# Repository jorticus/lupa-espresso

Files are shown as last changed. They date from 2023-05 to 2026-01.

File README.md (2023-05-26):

# LUPA ESPRESSO

ESP32 firmware for controlling my modified Vibiemme Domobar Junior, which is an E61-grouphead Heat Exchanger (HX) espresso machine.

The main goal is to add some smarts, but retain the manual control and analog feel.

NOTE: This project is not intended to be re-used on other machines as it is highly specific to the particular modifications I have made.

## Features

- PID control of heater boiler
- Automatic brew timer
- Digital pressure / temperature / flow readouts
- Graphing and gauges displayed on two round TFT displays
- Grouphead temperature approximation
- Preheat/sleep states
- Remote control
- HomeAssistant integration

## Modifications

- Analog pressure dials replaced with round TFT displays
- Digital pressure transducer
- Water flow sensor
- Platinum PT100 thermocouple probe
- Boiler SSR controlled by ESP32

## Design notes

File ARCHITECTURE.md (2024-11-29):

# Task Overview

## Core 0 : RF/Radio

## Core 1 : Arduino loop()

### Tasks:

- CoreIO : Priority 3, 1ms tick
  - GPIO handling
  - State machine
  - PID control loops
        
- Network : Priority 2, 10ms tick
  - WiFi reconnection logic
  - MQTT reconnection logic
  - HomeAssistant publishing
  - OTA

- UI : Priority 1
  - Idle loop (exeucte when no other tasks running)
  - Render
  - Display Update

- loop() : Priority 1
  - Failsafe code execution only.

### Timers:

- Timer 1 : 10ms
  - Pressure

- Timer 2 : 100ms
  - Temperature RTD 1 & 2
  - Water Low GPIO
  - Pulse Counter 1 & 2
  - Update graph samples

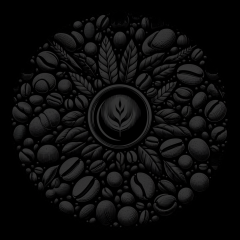
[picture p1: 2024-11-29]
img/RGB565/bean_bg2b.png

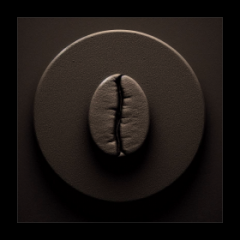
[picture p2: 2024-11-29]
img/RGB565/bg_coffee_eye_2.png

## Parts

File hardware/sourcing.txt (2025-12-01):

High voltage parts:
https://nz.element14.com/vigortronix/vtx-215-005-003/power-supply-ac-dc-3-3v-1a/dp/3870399
https://nz.element14.com/multicomp-pro/mcksk450m100g17s/capacitor-alu-elec-10uf-450v-radial/dp/2610819
https://nz.element14.com/panasonic-electric-works/aqh1213aj/ssr-600v-0-6a/dp/2095712
https://nz.element14.com/schurter/3404-2416-11/fuse-smd-umz-250-1a/dp/1829461
https://nz.element14.com/multicomp-pro/mor03sj0150a19/res-15r-5-3w-axial-metal-oxide/dp/1357899
https://nz.element14.com/kemet/a750kk827m0jaae016/cap-820-f-6-3v-20/dp/2614008

ESP32:
https://www.lcsc.com/product-detail/C328062.html?s_z=n_ESP32-WROOM-32U

Modules:
https://www.aliexpress.com/item/1005006704297164.html MAX RTD temperature converter module
https://www.aliexpress.com/item/1005004962049197.html 2x Round Display
https://www.aliexpress.com/item/4000411199411.html 2x Water flow sensor
https://www.aliexpress.com/item/1005004349225653.html 1x pressure sensor: G1/8 thread, 0-12Bar, I2C Output (or other thread to suit your machine)
https://www.aliexpress.com/item/32954468941.html 2x RTD temperature sensors:
    1x PT100, L 50mm, 1/4"
    1x PT100, L 100mm, 1/4"

Connectors:
https://nz.element14.com/multicomp-pro/mp001801/wtb-conn-header-8pos-1row-2-5mm/dp/3287578
https://nz.element14.com/multicomp-pro/mp001809/wtb-conn-header-r-a-2pos-1row/dp/3287588
https://nz.element14.com/multicomp-pro/mp001797/wtb-conn-header-4pos-1row-2-5mm/dp/3287574
https://nz.element14.com/multicomp-pro/mp001838/contact-socket-crimp-28-22awg/dp/3287624
https://nz.element14.com/multicomp-pro/mp001795/wtb-conn-header-2pos-1row-2-5mm/dp/3287572
https://nz.element14.com/multicomp-pro/mp001829/wtb-housing-rcpt-8pos-1row-2-5mm/dp/3287611
https://nz.element14.com/multicomp-pro/mp001823/wtb-housing-rcpt-2pos-1row-2-5mm/dp/3287603
https://nz.element14.com/multicomp-pro/mp001825/wtb-housing-rcpt-4pos-1row-2-5mm/dp/3287605

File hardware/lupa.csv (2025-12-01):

Reference | Qty | Value | DNP | Exclude from BOM | Exclude from Board | Footprint | Datasheet
C1
C6
C8 | 1 | 820uF 6.3V |  |  |  | Capacitor_THT:CP_Radial_D8.0mm_P3.50mm | ~
C9 | 1 | 1uF |  |  |  | Capacitor_SMD:C_0603_1608Metric | ~
C10 | 1 | 1nF 400V Y |  |  |  | Capacitor_THT:C_Rect_L7.0mm_W2.5mm_P5.00mm | ~
C12 | 1 | 100nF X2 |  |  |  | Capacitor_THT:C_Disc_D4.7mm_W2.5mm_P5.00mm | ~
C13 | 1 | 100uF |  |  |  | Capacitor_THT:CP_Radial_D5.0mm_P2.50mm | ~
C14 | 1 | 10uF 450V |  |  |  | Capacitor_THT:CP_Radial_D10.0mm_P5.00mm | https://4donline.ihs.com/images/VipMasterIC/IC/SCMP/SCMP-S-A0009021038/SCMP-S-A0009021038-1.pdf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
D1 | 1 | SMBJ7A |  |  |  | Diode_SMD:D_SMB | https://www.st.com/resource/en/datasheet/sm6t.pdf
F1 | 1 | 1A 250V |  |  |  | Fuse:Fuse_Schurter_UMZ250 | https://www.farnell.com/datasheets/3975405.pdf
FB1 | 1 | Ferrite |  |  |  | Resistor_SMD:R_0603_1608Metric | ~
J1 | 1 | LEVER |  |  |  | Connector_JST:JST_XH_B2B-XH-A_1x02_P2.50mm_Vertical | ~
J2 | 1 | POWER_BTN |  |  |  | Connector_JST:JST_XH_B2B-XH-A_1x02_P2.50mm_Vertical | ~
J3 | 1 | LOW_WATER |  |  |  | Connector_JST:JST_XH_B2B-XH-A_1x02_P2.50mm_Vertical | ~
J4 | 1 | FLOW1 |  |  |  | Connector_JST:JST_XH_B4B-XH-A_1x04_P2.50mm_Vertical | ~
J5 | 1 | FLOW2 |  |  |  | Connector_JST:JST_XH_B4B-XH-A_1x04_P2.50mm_Vertical | ~
J6 | 1 | PRESSURE1 |  |  |  | Connector_JST:JST_XH_B4B-XH-A_1x04_P2.50mm_Vertical | ~
J7 | 1 | PRESSURE2 |  |  |  | Connector_JST:JST_XH_B4B-XH-A_1x04_P2.50mm_Vertical | ~
J8 | 1 | LCD_L |  |  |  | Connector_JST:JST_XH_B8B-XH-A_1x08_P2.50mm_Vertical | ~
J9 | 1 | LCD_R |  |  |  | Connector_JST:JST_XH_B8B-XH-A_1x08_P2.50mm_Vertical | ~
J10 | 1 | LED_PWR |  |  |  | Connector_JST:JST_XH_B2B-XH-A_1x02_P2.50mm_Vertical | ~
J11 | 1 | MAX31865 |  |  |  | Connector_PinHeader_2.54mm:PinHeader_1x08_P2.54mm_Vertical | ~
J12 | 1 | POWER |  |  |  | Connector_JST:JST_XH_B2B-XH-A_1x02_P2.50mm_Vertical | ~
J13 | 1 | PROG |  |  |  | Connector_PinHeader_2.54mm:PinHeader_1x06_P2.54mm_Vertical_SMD_Pin1Left | ~
J14 | 1 | BOILER_SSR |  |  |  | Connector_JST:JST_XH_S2B-XH-A_1x02_P2.50mm_Horizontal | ~
J15
J16 | 1 | Mains |  |  |  | TerminalBlock_Altech:Altech_AK300_1x03_P5.00mm_45-Degree | ~
J17 | 1 | Fill Solenoid |  |  |  | TerminalBlock_Altech:Altech_AK300_1x02_P5.00mm_45-Degree | ~
J18 | 1 | Pump |  |  |  | TerminalBlock_Altech:Altech_AK300_1x02_P5.00mm_45-Degree | ~
J19 | 1 | Water Level |  |  |  | Connector_JST:JST_XH_B2B-XH-A_1x02_P2.50mm_Vertical | ~
L1 | 1 | 4.7mH |  |  |  | Inductor_THT:L_Radial_D6.0mm_P4.00mm | ~
L2 | 1 | 4.7uH 2.2A |  |  |  | Inductor_SMD:L_6.3x6.3_H3 | ~
Q1 | 1 | 2N7002 |  |  |  | Package_TO_SOT_SMD:SOT-23 | https://www.onsemi.com/pub/Collateral/NDS7002A-D.PDF
R1 | 1 | 10R |  |  |  | Resistor_SMD:R_0603_1608Metric | ~
R2
R5
R8
R16 | 1 | 12R 3W |  |  |  | Resistor_THT:R_Axial_DIN0516_L15.5mm_D5.0mm_P5.08mm_Vertical | https://www.farnell.com/datasheets/3110733.pdf
R22
RV1 | 1 | MOV |  |  |  | Capacitor_THT:C_Disc_D4.7mm_W2.5mm_P5.00mm
U1 | 1 | ESP32-WROOM-32U |  |  |  | RF_Module:ESP32-WROOM-32U | https://www.espressif.com/sites/default/files/documentation/esp32-wroom-32d_esp32-wroom-32u_datasheet_en.pdf
U2 | 1 | VTX-215-005-003 |  |  |  | Visclib:SMPS-VTX-215-005-003 | https://www.farnell.com/datasheets/3621164.pdf
U3

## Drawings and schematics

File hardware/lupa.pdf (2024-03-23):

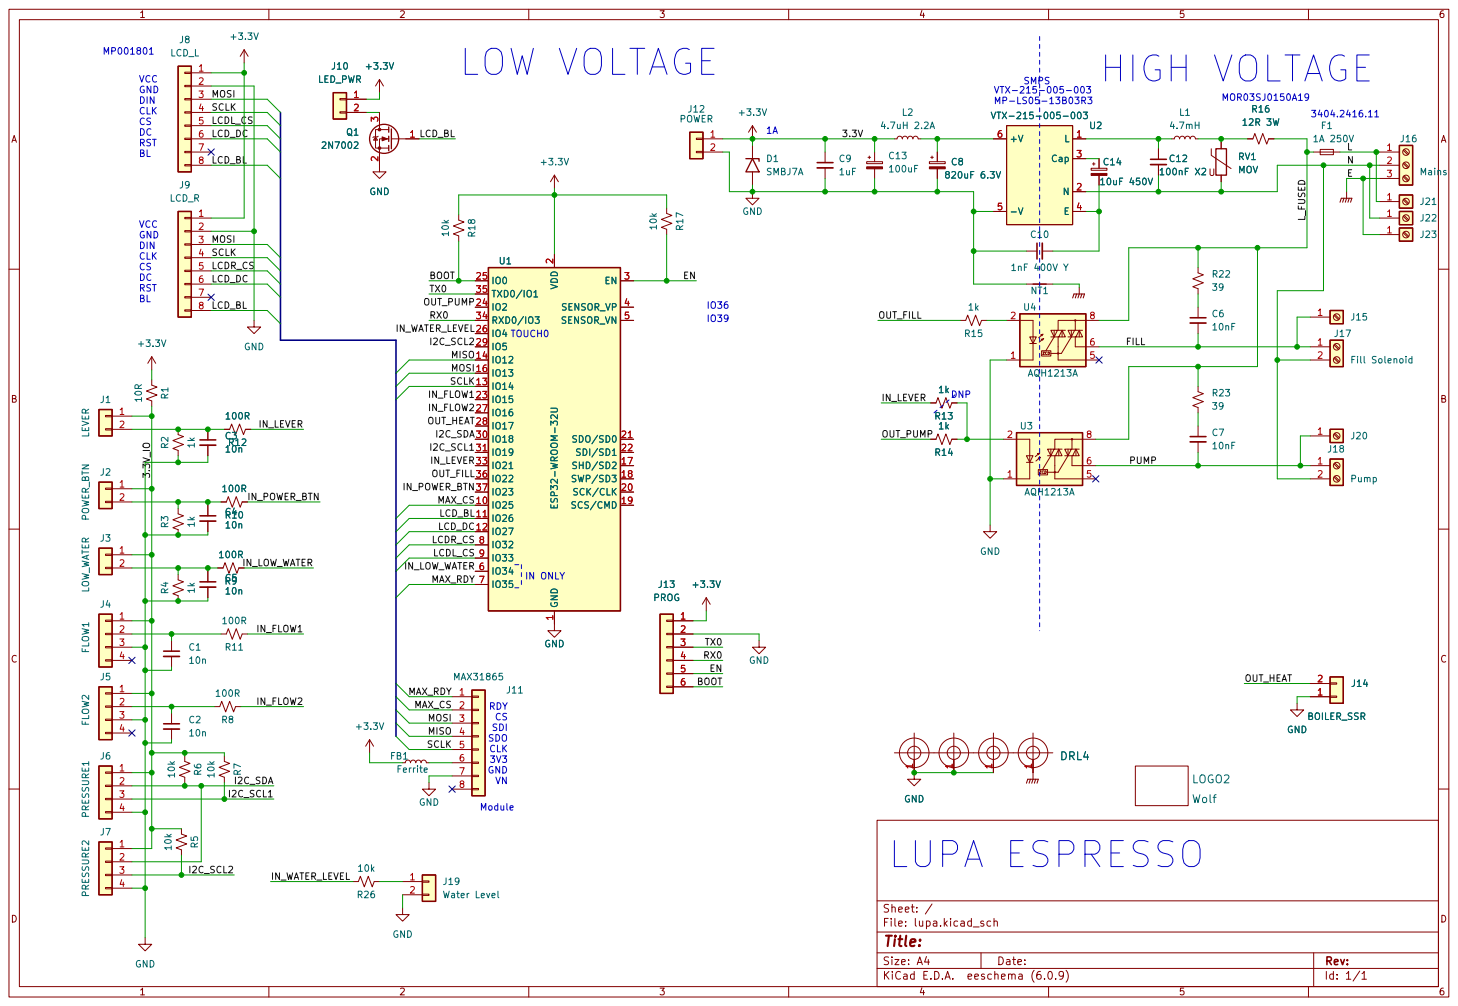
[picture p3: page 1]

SCLK LOW VOLTAGE
VTX-215-005-003 MP-LS05-13B03R3 SMPS LUPA ESPRESSO

2 SCK/CLK 20 SDO/SD0 21 SDI/SD1 22

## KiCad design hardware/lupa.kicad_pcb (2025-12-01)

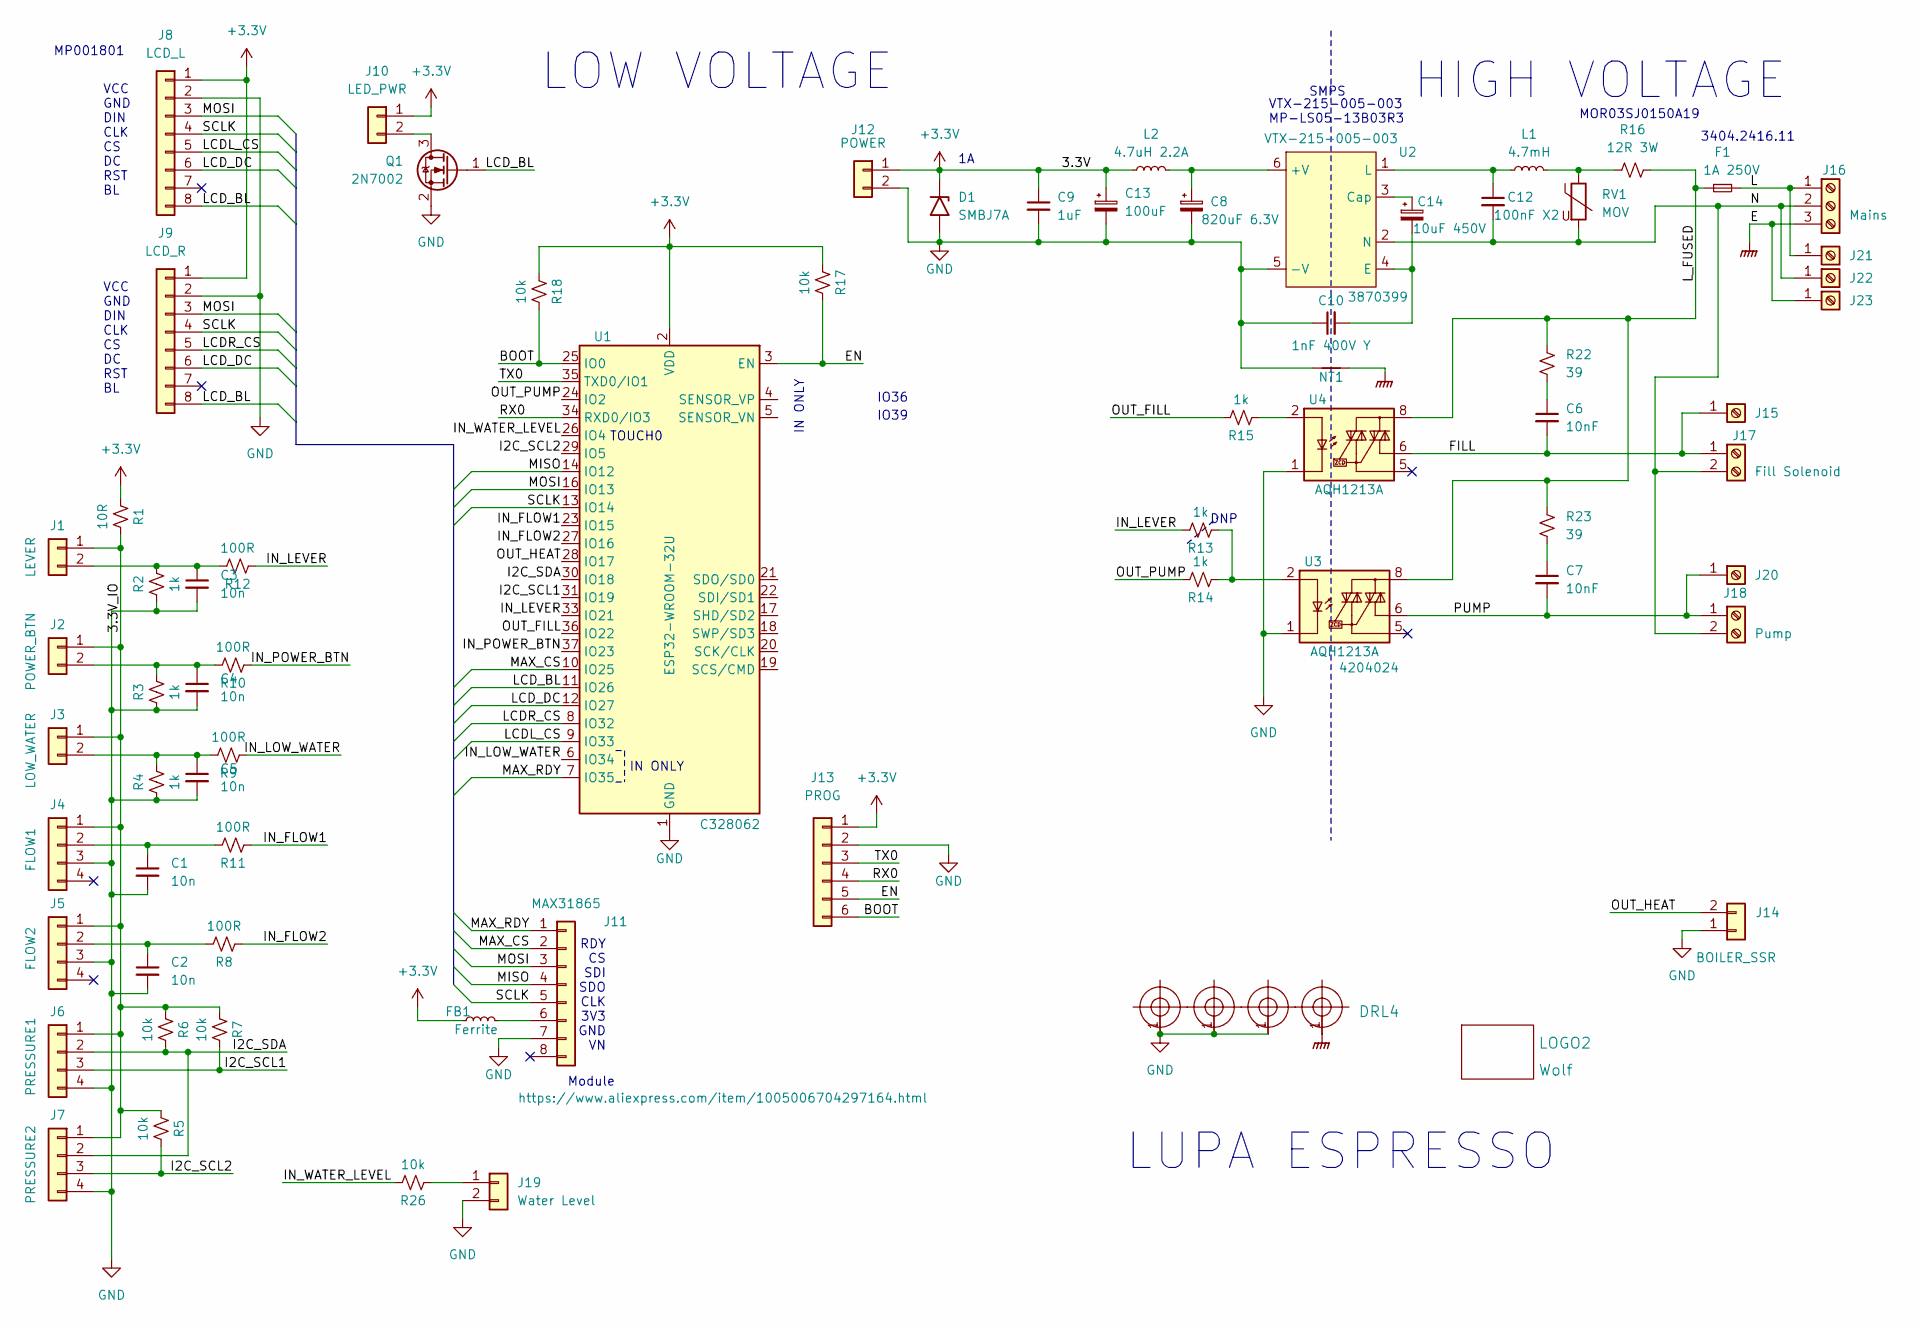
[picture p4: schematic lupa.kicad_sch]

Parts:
C1, C2, C3, C4, C5: 10n; C_0603_1608Metric
C6, C7: 10nF; R_0805_2012Metric
C8: 820uF 6.3V; CP_Radial_D8.0mm_P3.50mm; Farnell 2614008
C9: 1uF; C_0603_1608Metric
C10: 1nF 400V Y; C_Rect_L7.0mm_W2.5mm_P5.00mm
C12: 100nF X2; C_Disc_D4.7mm_W2.5mm_P5.00mm
C13: 100uF; CP_Radial_D5.0mm_P2.50mm
C14: 10uF 450V; CP_Radial_D10.0mm_P5.00mm; Farnell 2610819
D1: SMBJ7A; D_SMB
DRL1, DRL2, DRL3, DRL4: DrillHoleE; MountingHole_3.2mm_M3_Pad
F1: 1A 250V; Fuse_Schurter_UMZ250; Farnell 1829461
FB1: Ferrite; R_0603_1608Metric
J1: LEVER; JST_XH_B2B-XH-A_1x02_P2.50mm_Vertical; Farnell 3287572
J2: POWER_BTN; JST_XH_B2B-XH-A_1x02_P2.50mm_Vertical; Farnell 3287572
J3: LOW_WATER; JST_XH_B2B-XH-A_1x02_P2.50mm_Vertical; Farnell 3287572
J4: FLOW1; JST_XH_B4B-XH-A_1x04_P2.50mm_Vertical; Farnell 3287574
J5: FLOW2; JST_XH_B4B-XH-A_1x04_P2.50mm_Vertical; Farnell 3287574
J6: PRESSURE1; JST_XH_B4B-XH-A_1x04_P2.50mm_Vertical; Farnell 3287574
J7: PRESSURE2; JST_XH_B4B-XH-A_1x04_P2.50mm_Vertical; Farnell 3287574
J8: LCD_L; JST_XH_B8B-XH-A_1x08_P2.50mm_Vertical; Farnell 3287578
J9: LCD_R; JST_XH_B8B-XH-A_1x08_P2.50mm_Vertical; Farnell 3287578
J10: LED_PWR; JST_XH_B2B-XH-A_1x02_P2.50mm_Vertical; Farnell 3287572
J11: MAX31865; PinHeader_1x08_P2.54mm_Vertical
J12: POWER; JST_XH_B2B-XH-A_1x02_P2.50mm_Vertical; Farnell 3287572
J13: PROG; PinHeader_1x06_P2.54mm_Vertical_SMD_Pin1Left
J14: BOILER_SSR; JST_XH_S2B-XH-A_1x02_P2.50mm_Horizontal; Farnell 3287588
J15, J20, J21, J22, J23: Screw_Terminal_01x01; TAB_TERMINAL
J16: Mains; Altech_AK300_1x03_P5.00mm_45-Degree
J17: Fill Solenoid; Altech_AK300_1x02_P5.00mm_45-Degree
J18: Pump; Altech_AK300_1x02_P5.00mm_45-Degree
J19: Water Level; JST_XH_B2B-XH-A_1x02_P2.50mm_Vertical; Farnell 3287572
L1: 4.7mH; L_Radial_D6.0mm_P4.00mm
L2: 4.7uH 2.2A; L_6.3x6.3_H3
LOGO2: Wolf; wolfpaw-0.3
NT1: NetTie_2; NetTie-2_SMD_Pad2.0mm
Q1: 2N7002; SOT-23
R1: 10R; R_0603_1608Metric
R2, R3, R4, R13, R14, R15: 1k; R_0603_1608Metric
R5, R6, R7, R17, R18, R26: 10k; R_0603_1608Metric
R8, R9, R10, R11, R12: 100R; R_0603_1608Metric
R16: 12R 3W; R_Axial_DIN0516_L15.5mm_D5.0mm_P5.08mm_Vertical; Farnell 1357899
R22, R23: 39; R_0805_2012Metric
RV1: MOV; C_Disc_D4.7mm_W2.5mm_P5.00mm
U1: ESP32-WROOM-32U; LCSC C328062
U2: VTX-215-005-003; SMPS-VTX-215-005-003; Farnell 3870399
U3, U4: AQH1213A; SSO-7-8_6.4x9.78mm_P2.54mm; Mouser 769-AQH1213A

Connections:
+3.3V: C9.1, C13.1, D1.1 (A1), FB1.1, J8.1, J9.1, J10.1, J12.1, J13.1, L2.1, R1.1, R17.1, R18.1, U1.2 (VDD)
/3.3V_IO: J1.1, J2.1, J3.1, J4.1, J5.1, J6.1, J7.1, R1.2, R5.1, R6.1, R7.1
/BOOT: J13.6, R18.2, U1.25 (IO0)
/EN: J13.5, R17.2, U1.3 (EN)
/FILL: C6.2, J15.1, J17.1, U4.6
/I2C_SCL1: J6.3, R7.2, U1.31 (IO19)
/I2C_SCL2: J7.3, R5.2, U1.29 (IO5)
/I2C_SDA: J6.2, J7.2, R6.2, U1.30 (IO18)
/IN_FLOW1: R11.1, U1.23 (IO15)
/IN_FLOW2: R8.1, U1.27 (IO16)
/IN_LEVER: R12.1, R13.2, U1.33 (IO21)
/IN_LOW_WATER: R9.1, U1.6 (IO34)
/IN_POWER_BTN: R10.1, U1.37 (IO23)
/IN_WATER_LEVEL: R26.2, U1.26 (IO4)
/L: F1.2, J16.1, J21.1
/LCDL_CS: J8.5, U1.9 (IO33)
/LCDR_CS: J9.5, U1.8 (IO32)
/LCD_BL: J8.8, J9.8, Q1.1 (G), U1.11 (IO26)
/LCD_DC: J8.6, J9.6, U1.12 (IO27)
/L_FUSED: F1.1, R16.2, R22.1, R23.1, U3.8, U4.8
/MAX_CS: J11.2, U1.10 (IO25)
/MAX_RDY: J11.1, U1.7 (IO35)
/MISO: J11.4, U1.14 (IO12)
/MOSI: J8.3, J9.3, J11.3, U1.16 (IO13)
/N: C12.2, J16.2, J17.2, J18.2, J22.1, RV1.2, U2.2 (N)
/OUT_FILL: R15.2, U1.36 (IO22)
/OUT_HEAT: J14.2, U1.28 (IO17)
/OUT_PUMP: R14.2, U1.24 (IO2)
/PUMP: C7.2, J18.1, J20.1, U3.6
/RX0: J13.4, U1.34 (RXD0/IO3)
/SCLK: J8.4, J9.4, J11.5, U1.13 (IO14)
/TX0: J13.3, U1.35 (TXD0/IO1)
GND: C1.2, C2.2, C3.2, C4.2, C5.2, C8.2, C9.2, C10.1, C13.2, D1.2 (A2), DRL1.1, DRL2.1, DRL3.1, J4.3, J5.3, J6.4, J7.4, J8.2, J9.2, J11.7, J12.2, J13.2, J14.1, J19.2, NT1.1, Q1.2 (S), R2.1, R3.1, R4.1, U1.1 (GND), U1.15 (GND), U1.38 (GND), U1.39 (GND), U2.5 (-V), U3.1, U3.3, U3.4, U4.1, U4.3, U4.4
GNDPWR: DRL4.1, J16.3, J23.1, NT1.2
unnamed: C6.1, R22.2
unnamed: C7.1, R23.2
unnamed: C3.1, J1.2, R2.2, R12.2
unnamed: C4.1, J2.2, R3.2, R10.2
unnamed: C5.1, J3.2, R4.2, R9.2
unnamed: C1.1, J4.2, R11.2
unnamed: C2.1, J5.2, R8.2
unnamed: J10.2, Q1.3 (D)
unnamed: FB1.2, J11.6
unnamed: J19.1, R26.1
unnamed: L1.2, R16.1, RV1.1
unnamed: R13.1, R14.1, U3.2
unnamed: R15.1, U4.2
unnamed: C8.1, L2.2, U2.6 (+V)
unnamed: C14.1, U2.3 (Cap)
unnamed: C10.2, C14.2, U2.4 (E)
unnamed: C12.1, L1.1, U2.1 (L)

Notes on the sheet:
HIGH VOLTAGE
Module
LOW VOLTAGE
MOR03SJ0150A19
IN ONLY
RDY CS SDI SDO CLK 3V3 GND VN
TOUCH0
MP001801
SMPS
VCC GND DIN CLK CS DC RST BL
LUPA ESPRESSO
VTX-215-005-003 MP-LS05-13B03R3
DNP
IO39
IO36
3404.2416.11

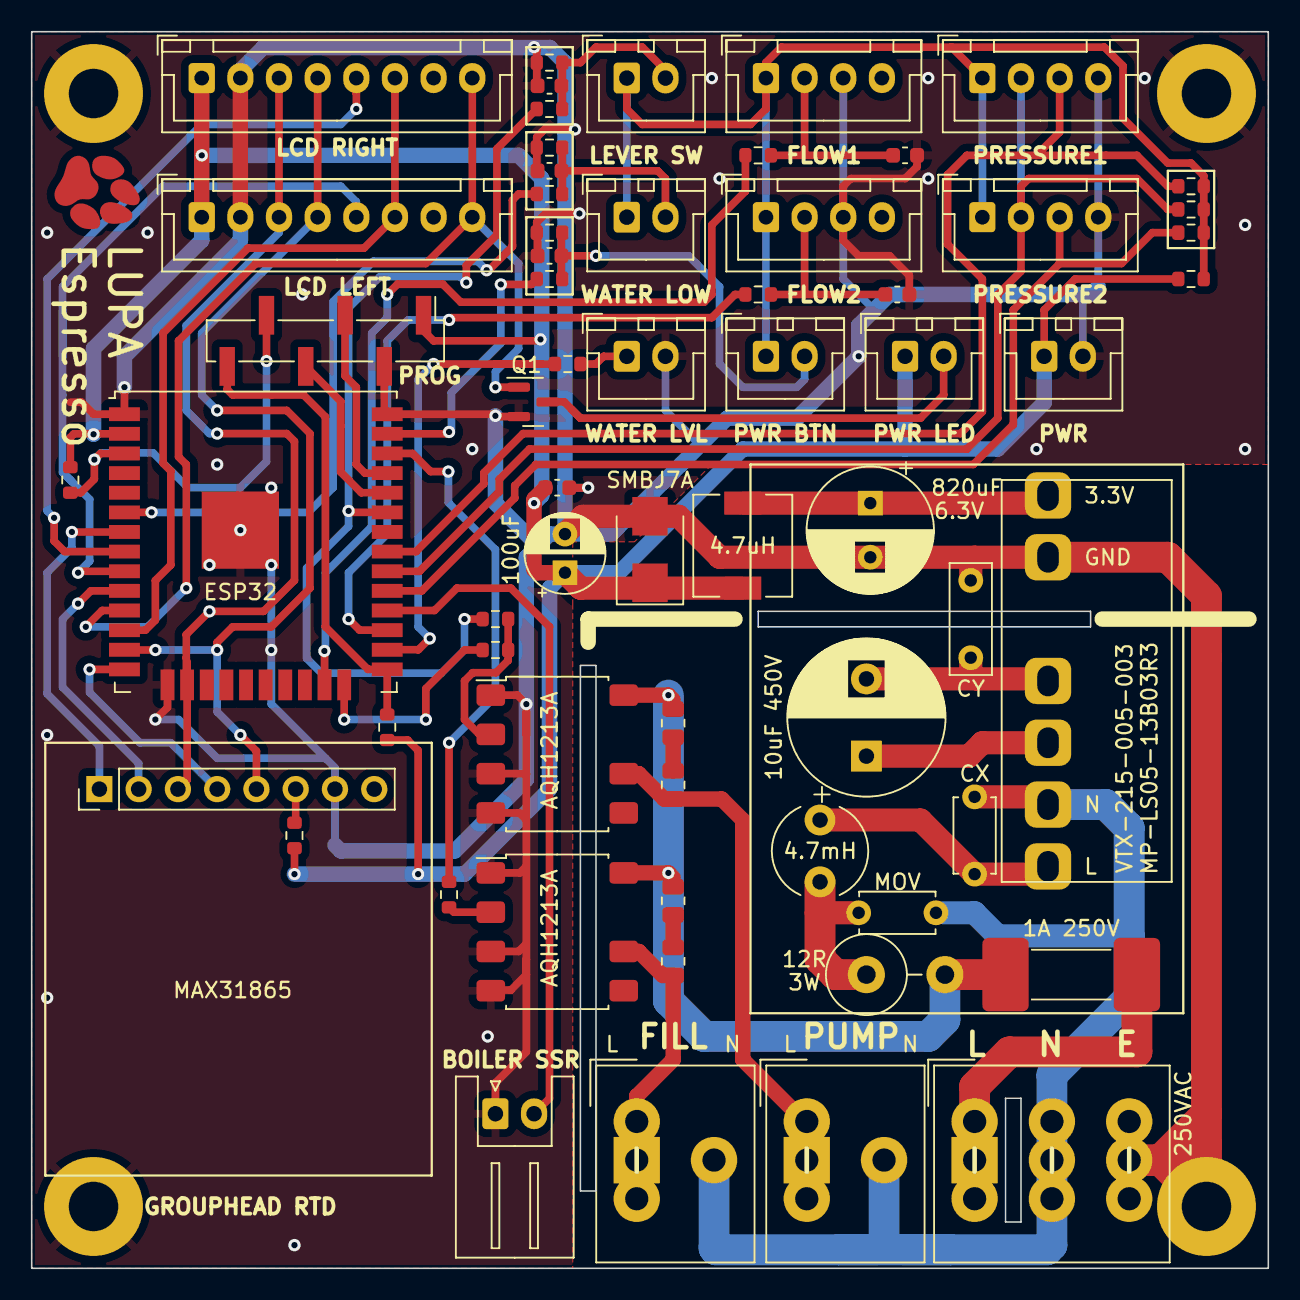
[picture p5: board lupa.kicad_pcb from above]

Board: 2 copper layers, 80.0 x 80.0 mm, 74 parts (0 on the bottom side), 51 nets.

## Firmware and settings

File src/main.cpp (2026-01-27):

#include <Arduino.h>
#include <Adafruit_MAX31865.h>
#include <TFT_eSPI.h>
#include <WiFi.h>
#include <SPIFFS.h>
#include "secrets.h"
#include "PressureTransducer.h"
#include "config.h"
#include "hardware.h"
#include "SensorSampler.h"
#include "IO.h"
#include "Debug.h"
#include "StateMachine.h"
#include "HeatControl.h"
#include "BrewControl.h"
#include "Display.h"
#include "UI.h"
#include "Net.h"
#include "OTA.h"
#include "HomeAssistant.h"
#include "Panic.h"
#include "Task.h"
#include "WebSrv.h"
#include <esp_task_wdt.h>

// NOTE: WiFiClient default timeout is 3 seconds, WDT should probably be longer than this.
const uint32_t WDT_TIMEOUT_SEC = 4;

extern SPIClass spi; // Defined in TFT_eSPI\Processors\TFT_eSPI_ESP32.c (HSPI)
extern TFT_eSPI tft; // Defined in Display.cpp

#if defined(LUPA_V1)
// MAX31865 shares SPI bus with TFT
Adafruit_MAX31865   rtd1(MAX1_CS, &spi);
Adafruit_MAX31865   rtd2(MAX2_CS, &spi);

#elif defined(LUPA_V2)
// MAX31865 on separate SPI bus (VSPI)
SPIClass spi2(VSPI);
Adafruit_MAX31865   rtd1(MAX1_CS, &spi2);
Adafruit_MAX31865   rtd2(MAX2_CS, &spi2);

#endif

PressureTransducer  pressure(PRESSURE_FULL_SCALE);


static TaskHandle_t task_core;
static TaskHandle_t task_network;
static TaskHandle_t task_ui;
static TaskHandle_t task_display;

static bool s_failsafe = true;

using namespace Display;

bool handle_reset() {
    auto reason = esp_reset_reason();
    Debug.printf("Reset Reason: %d\n", reason);
    if (reason == ESP_RST_PANIC || 
        reason == ESP_RST_INT_WDT ||
        reason == ESP_RST_WDT ||
        reason == ESP_RST_TASK_WDT)
    {
        Debug.print("Last reset was due to ");
        switch (reason) {
            case ESP_RST_PANIC:     Debug.print("FW Panic"); break;
            case ESP_RST_INT_WDT:   Debug.print("INT WDT"); break;
            case ESP_RST_WDT:       Debug.print("WDT"); break;
            case ESP_RST_TASK_WDT:  Debug.print("Task WDT"); break;
            default:                Debug.print(reason);
        }
        Debug.println(", entering failsafe mode...");

        if (reason == ESP_RST_PANIC) {
            print_panic_buffer();
            State::setFault(State::FaultState::SoftwarePanic, "PANIC");
        }
        else {
            State::setFault(State::FaultState::SoftwarePanic, "WATCHDOG");
        }

        clear_panic_buffer();

        return true;
    }
    else {
        clear_panic_buffer();
        return false;
    }
}

/**
 * Criticial initialization
 * Only initialize subsystems required for setting up OTA update and 
 * ensuring the system hardware is in a safe state
*/
bool initCritical() {
    Serial.begin(UART_DEBUG_BAUD);

    IO::initGpio();
    DebugLogger::init();

    Display::initDisplay();

    Net::initWiFi();
    OTA::initOTA();

    Serial.println("Critical init done");
    return true;
}

/**
 * Network Task (CORE 1, PRIORITY 2)
 * Handles all network connection logic.
 * Must be higher priority so it can preempt other tasks.
*/
void taskNetworkFunc(void* ctx) {
    Debug.println("Network Task Started");

    HomeAssistant::init();

    // TODO: quite memory hungry (~9KB)
    // We only have ~15KB to work with after the display buffers & MQTT subscriptions,
    // and we need around 10KB to accept an OTA update
    WebSrv::setup();

    while (true) {
        vTaskDelay(100 / portTICK_PERIOD_MS);
        Net::handle();

        if (Net::isConnected())
        {
            OTA::handle(); // May block

            DebugLogger::process();

            HomeAssistant::process();

            WebSrv::process();
        }
    }
}

/**
 * Core Task (CORE 1, PRIORITY 3) HIGH PRIORITY
 * Handles I/O, State Machine, Control Loops
*/
void taskCoreFunc(void* ctx) {
    Debug.println("Core Task Started");

    while (true) {
        vTaskDelay(1 / portTICK_PERIOD_MS);

        IO::process();

        SensorSampler::process();
        State::processState();

        if (State::uiState != State::MachineState::FirmwareUpdate && 
            State::uiState != State::MachineState::Off)
        {
            HeatControl::processControlLoop();
        }

    }
    //vTaskDelete(nullptr);
}

/**
 * Render Task (CORE 1, PRIORITY 1)
 * Handles rendering of UI.
 * Must be low priority so other tasks can preempt it.
*/
void taskRenderUiFunc(void* ctx) {
    Debug.println("Render Task Started");

    while (true) {
        taskYIELD();
        UI::render();
    }
}



void initSystem() {

    //
    // Non-critical initialization
    //

    IO::initPwm();
    //HomeAssistant::init();

    bool isSensorsInitialized = SensorSampler::initialize();

    HeatControl::initControlLoop();
    BrewControl::initControlLoop();

    SensorSampler::start();

    // // Initialize SPIFFS
    // Serial.println("Mount SPIFFS");
    // if (!SPIFFS.begin(true)) {
    //     Serial.println("Error mounting SPIFFS");
    // }
    
    // Power-on state:
    // State::setState(State::MachineState::UiTest);
    // State::setState(State::MachineState::SensorTest);
    State::setState(State::MachineState::Off);
    // State::setState(State::MachineState::Preheat);

#if 0
    // If sensors could not be initialized, indicate fault
    if (State::uiState != State::MachineState::SensorTest && 
       (!isSensorsInitialized))
    {
        State::setFault(State::FaultState::SensorFailure, "");
    }
#endif

    Serial.println("Start tasks");
    xTaskCreatePinnedToCore(taskCoreFunc,     "CoreTask", 3*1024, nullptr, TASK_PRIORITY_CORE,      &task_core,    CORE1);
    xTaskCreatePinnedToCore(taskNetworkFunc,  "NetTask",  4*1024, nullptr, TASK_PRIORITY_NETWORK,   &task_network, CORE1);
    xTaskCreatePinnedToCore(taskRenderUiFunc, "UiTask",   3*1024, nullptr, TASK_PRIORITY_UI,        &task_ui,      CORE1);

    Serial.println("System init done");
}

/**
 * Main setup entrypoint
*/
void setup() {
    // Disable watchdog during init to give system time to boot.
    // The WiFi especially can take a significant amount of time to connect.
    // esp_task_wdt_init(10, false);
    // esp_task_wdt_config_t wdt = {
    //     .timeout_ms = 10000,
    //     .idle_core_mask = 1, // TODO??
    //     .trigger_panic = false
    // };
    // esp_task_wdt_init(&wdt);

    delay(1000);

    if (!initCritical()) {
        State::setFault(State::FaultState::FailsafeRecovery);
        return;
    }

    // Enter fail-safe mode if we've encountered a firmware bug,
    // before proceeding further. This allows us to recover via OTA.
    if (handle_reset()) {
        return;
    }
    // Holding power button on reset will also enter recovery mode.
    if (digitalRead(PIN_IN_POWER_BTN) == HIGH) {
        while (digitalRead(PIN_IN_POWER_BTN) == HIGH) continue;
        State::setFault(State::FaultState::FailsafeRecovery);
        return;
    }
#if defined(FAILSAFE_RECOVERY)
    // Building with this flag set will always enter recovery mode.
    State::setFault(State::FaultState::FailsafeRecovery);
    return;
#endif
    s_failsafe = false;

    initSystem();

    // Enable watchdog timer
    // Serial.println("Enable WDT");
    // esp_task_wdt_config_t wdt = {
    //     .timeout_ms = 10000,
    //     .idle_core_mask = 1, // ??
    //     .trigger_panic = false
    // };
    // wdt.timeout_ms = WDT_TIMEOUT_SEC * 1000UL;
    // wdt.trigger_panic = true;
    // esp_task_wdt_init(&wdt);
    // esp_task_wdt_add(NULL); //add current thread to WDT watch

    Debug.println("Done!");
}

/**
 * Background RTOS task (CORE 1, PRIORITY 1)
*/
void loop()
{
    // esp_task_wdt_reset();
    taskYIELD();

    // Heap monitor
    static long t_last = 0;
    static uint32_t heap_last = 0;
    if ((millis() - t_last) > 100) {
        t_last = millis();
        auto heap = esp_get_free_heap_size();
        // if (heap != heap_last) {
        //     int32_t delta = (int32_t)heap - (int32_t)heap_last;
        //     Debug.printf("HEAP: %d (%d)\n", heap, delta);
        //     heap_last = heap;
        // }

        if (heap < 1024) {
            Debug.printf("WARNING: LOW MEMORY (%d bytes)\n", heap);
            State::setFault(State::FaultState::SoftwarePanic, "OOM");
            delay(500);
            abort();
        }
    }

    // Failsafe idle loop
    // This ensures the system can continue to receive firmware updates.
    if (s_failsafe) {
        IO::process();
        Net::handle();

        if (Net::isConnected())
        {
            OTA::handle();
            DebugLogger::process();
        }

        UI::renderFailsafe();
    }
}

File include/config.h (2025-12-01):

#pragma once

// Target heat exchanger (HX) temperature for brewing (BoilerProfile::Brew)
// Typically this is 5C lower than the main boiler.
#define CONFIG_BOILER_TEMPERATURE_C (115.0f) // ~95C on grouphead
//#define CONFIG_BOILER_TEMPERATURE_C (117.0f) // ~96C on grouphead
//#define CONFIG_BOILER_TEMPERATURE_C (120.0f) // ~97C on grouphead
//#define CONFIG_BOILER_TEMPERATURE_C (125.0f) // ~94C on grouphead according to manual

// Target boiler temperature for steaming (BoilerProfile::Steam)
// #define CONFIG_BOILER_STEAM_TEMPERATURE_C (125.0f)
#define CONFIG_BOILER_STEAM_TEMPERATURE_C (120.0f)

// Target boiler temperature in idle mode (BoilerProfile::Idle)
#define CONFIG_BOILER_IDLE_TEMPERATURE_C (60.0f)

// Target boiler temperature for PID tuning (BoilerProfile::Tuning)
#define CONFIG_BOILER_TUNING_TEMPERATURE_C (110.f)

// Range at which the PID controller is active
// relative to the current PID setpoint
#define CONFIG_BOILER_PID_RANGE_C (20.0f)

// Maximum boiler temperature
// Heat control loop will be disabled above this temperature.
// Important: This does not replace the need for a hardware safety cutoff!
// The VBM Domobar HX has three safety cutoffs - 
// A. the pressurestat will regulate the upper temperature
// B. the over pressure valve on the boiler will release steam if pressure exceeds safe limits
// C. the thermal fuse will blow if the boiler exterior exceeds safe limits
// #define CONFIG_MAX_BOILER_TEMPERATURE_C (130.0f)
#define CONFIG_MAX_BOILER_TEMPERATURE_C (125.0f)

// Target preheat temperature
// Defines when to exit the preheat phase and become ready.
// Does not control actual target temperature, only controls for how
// long the preheat UI is shown.
#define CONFIG_BOILER_PREHEAT_TARGET_C (CONFIG_BOILER_TEMPERATURE_C - 5.0f)

// Minimum system pressure
// Machine will attempt to keep pressure above this level when idle
#define CONFIG_MIN_PRESSURE (0.5f)
#define CONFIG_MAX_PRESSURE (12.0f)

// Target brew pressure
#define CONFIG_TARGET_BREW_PRESSURE (10.0f)

// Machine idle timeout
//#define CONFIG_IDLE_TIMEOUT_MS (0) // Disabled
//#define CONFIG_IDLE_TIMEOUT_MS (30*60*1000) // 30m
//#define CONFIG_IDLE_TIMEOUT_MS (2*60*60*1000) // 2h
#define CONFIG_IDLE_TIMEOUT_MS (2*60*60*1000) // 1h
//#define CONFIG_IDLE_TIMEOUT_MS (60*1000) // 1m

// Fault clear timeout
#define CONFIG_FAULT_CLEAR_TIMEOUT_MS (30*60*1000) // 30sec

// If true, put device into power-saving mode as soon as it is
// up to temperature. 
#define CONFIG_IDLE_AFTER_PREHEAT (false)

// Brew finish timeout
// Time before post-brew screen disappears and is replaced with the Ready screen
#define CONFIG_BREW_FINISH_TIMEOUT_MS (60*1000)

#define CONFIG_FULL_BRIGHTNESS (1.0f)
#define CONFIG_IDLE_BRIGHTNESS (0.2f)

// Whether to wait for WiFi connection on startup
#define CONFIG_WAIT_FOR_WIFI (false)

// Perform PID tuning process instead of usual logic
#define CONFIG_DO_PID_TUNE (false)

// Measured power of boiler in watts,
// used for estimating energy consumption
#define CONFIG_BOILER_FULL_POWER_WATTS (1333.0f)

// Whether to enable pressure profiling (PID control of pressure during brew)
#define CONFIG_ENABLE_PRESSURE_PROFILING (true)

// Maximum pressure range to display
#define PRESSURE_UI_MAX_BAR (10.0f)

// Maximum flowrate for water flow sensor (mL/s) to display
//#define FLOW_UI_MAX_VALUE (15.0f)
#define FLOW_UI_MAX_VALUE (5.0f)

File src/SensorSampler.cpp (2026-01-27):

#include <Arduino.h>
#include <freertos/semphr.h>
#include "SensorSampler.h"
#include "StateMachine.h"
#include "Debug.h"

#include "value_array.h"
#include "fir.h"

#include "hardware.h"
#include "Adafruit_MAX31865.h"
#include "PressureTransducer.h"
#include "PulseCounter.h"
#include "BrewControl.h"
#include "Task.h"
#include "config.h"


#define PREHEAT_TEMPERATURE_C (CONFIG_BOILER_TEMPERATURE_C - 5.0f)

extern Adafruit_MAX31865   rtd1;
extern Adafruit_MAX31865   rtd2;
extern PressureTransducer  pressure;

#if defined(LUPA_V1)
volatile bool g_isWaterTankLow = false;
#endif

namespace SensorSampler {

// Circular buffers for storing historical sensor readings.
// These are used to render graphs in the UI
ValueArray<float, numSamples> temperatureSamples;
ValueArray<float, numSamples> temperatureSamples2;
ValueArray<float, numSamples> pressureSamples;
ValueArray<float, numSamples> flowSamples;

static int waterTankDebounce = 0;

static bool isTemperature1Available = false;
static bool isTemperature2Available = false;
static bool isPressureAvailable = false;
static bool isFlowAvailable = false;

static bool s_isFlowing = false;

// https://wirelesslibrary.labs.b-com.com/FIRfilterdesigner/#/#result-container
static const float filter_21tap_10hz[] = {
    // 0.5-10Hz @ 100Hz sample
    0.00434242941534996,0.008949466084110017,0.015604865894648115,0.025553833195889674,0.03669107854100511,0.04997034706423948,0.06273586677719478,0.07524549489402194,0.08472427725410565,0.09148873683644758,0.09336684579062392,0.09148873683644758,0.08472427725410565,0.07524549489402194,0.06273586677719478,0.04997034706423948,0.03669107854100511,0.025553833195889674,0.015604865894648115,0.008949466084110017,0.00434242941534996
};

static const float filter_41tap_20hz[] = {
    0.000013852416495175956,-0.0005731238127494758,-0.0009721997930380986,-0.00039876522390940147,0.0015930558424190862,0.0035931092532572894,0.002749971869114803,-0.0023913231618499036,-0.00876755135029208,-0.009422988391486293,0.0004666650013959363,0.01636373968020993,0.023898422721952334,0.009361110013097404,-0.02483789795201317,-0.05355958127324209,-0.04126902294878148,0.03159907402929509,0.14754130006838131,0.25526633301692403,0.29914396401895105,0.25526633301692403,0.14754130006838131,0.03159907402929509,-0.04126902294878148,-0.05355958127324209,-0.02483789795201317,0.009361110013097404,0.023898422721952334,0.01636373968020993,0.0004666650013959363,-0.009422988391486293,-0.00876755135029208,-0.0023913231618499036,0.002749971869114803,0.0035931092532572894,0.0015930558424190862,-0.00039876522390940147,-0.0009721997930380986,-0.0005731238127494758,0.000013852416495175956
};

static const float filter_21tap_20hz[] = {
    // Sample rate: 10Hz
    // Symmetric, 21 taps
    // Pass Band: 0-2Hz, 0.1 ripple
    // Stop Band: 2.5-5Hz, -40dB
    0.03545137019649825,-0.0022262708339058795,-0.034990888681942306,-0.021822371807547182,0.03237086731810076,0.03566348010931214,-0.048490211874641614,-0.09471486749562563,0.045288533737803296,0.30932157253256914,0.4456425549907703,0.30932157253256914,0.045288533737803296,-0.09471486749562563,-0.048490211874641614,0.03566348010931214,0.03237086731810076,-0.021822371807547182,-0.034990888681942306,-0.0022262708339058795,0.03545137019649825
};

static const float filter_21tap_1Hz[] = {
    // Sample rate: 10Hz
    // Symmetric, 21 taps
    // Pass Band: 0-1Hz, 1Hz ripple
    // Stop Band: 2.5-5Hz, -60dB
    0.001465356455737356,0.005946307256892348,0.010949886826641072,0.007317673377397633,-0.012924269445836039,-0.04020894607521747,-0.04139075948899614,0.018310463615369015,0.13680053545393453,0.2593177467532354,0.3116728085909527,0.2593177467532354,0.13680053545393453,0.018310463615369015,-0.04139075948899614,-0.04020894607521747,-0.012924269445836039,0.007317673377397633,0.010949886826641072,0.005946307256892348,0.001465356455737356
};

static const float filter_21tap_1p2Hz[] = {
    // Sample rate: 10Hz
    // Symmetric, 21 taps
    // Pass Band: 0-0.5Hz, 1Hz ripple
    // Stop Band: 1.2-5Hz, -60dB
    -0.0001765242939152268,0.004401257856427506,0.011006069982754735,0.022423968669624268,0.03866768524989652,0.059048935435686956,0.0818098105491962,0.10429767844259977,0.12342079736957758,0.1362809596254636,0.14081655316434108,0.1362809596254636,0.12342079736957758,0.10429767844259977,0.0818098105491962,0.059048935435686956,0.03866768524989652,0.022423968669624268,0.011006069982754735,0.004401257856427506,-0.0001765242939152268
};

static const float filter_11tap_1hz[] = {
    // Sample rate: 10Hz
    // Symmetric, 11 taps
    // Pass Band: 0-1Hz, 0.1Hz ripple
    // Stop Band: 2.5-5Hz, -60dB
    // NOTE: Using 11 taps gives us a faster response time
    -0.017761211782565366,-0.023388527987987403,0.02182651994577536,0.13593660665383586,0.2678079051444623,0.32697267711600697,0.2678079051444623,0.13593660665383586,0.02182651994577536,-0.023388527987987403,-0.017761211782565366
};

static const float filter_11tap_0p5hz[] = {
    // Sample rate: 10Hz
    // Symmetric, 11 taps
    // Pass Band: 0-0.6Hz, 0.5Hz ripple
    // Stop Band: 1-5Hz, -40dB
    0.06750407977332626,0.06447378522564463,0.08602036182482176,0.10434577815450256,0.11664142455124397,0.12098301069687106,0.11664142455124397,0.10434577815450256,0.08602036182482176,0.06447378522564463,0.06750407977332626
};

static const float filter_11tap_2hz[] = {
    // Sample rate: 100Hz
    // Symmetric, 11 taps
    // Pass Band: 0-2Hz, 0.5Hz ripple
    // Stop Band: 20-50Hz, -40dB
    0.008781172584127157,0.03397045986906245,0.07521111897851179,0.1272020312087974,0.16957364237449396,0.18701713727754435,0.16957364237449396,0.1272020312087974,0.07521111897851179,0.03397045986906245,0.008781172584127157
};

static const float filter_21tap_5hz[] = {
    0.04970840507037454,0.02432910126303465,0.029393020463172576,0.034442051358810365,0.03929393287595301,0.04379242949355152,0.04772232341361974,0.05097417933381713,0.05339159902528805,0.05488367919912227,0.055399526352131044,0.05488367919912227,0.05339159902528805,0.05097417933381713,0.04772232341361974,0.04379242949355152,0.03929393287595301,0.034442051358810365,0.029393020463172576,0.02432910126303465,0.04970840507037454
};

// Automatic FIR filters of type FirFilter<N_TAPS> { taps }
static auto filter_pressure     = MAKE_FIR_FILTER(filter_21tap_10hz);
static auto filter_temperature_1  = MAKE_FIR_FILTER(filter_21tap_10hz);   
static auto filter_temperature_2  = MAKE_FIR_FILTER(filter_21tap_10hz);   

static auto filter_flowrate     = MAKE_FIR_FILTER(filter_11tap_1hz);    // 10Hz sample
static auto filter2_flowrate     = MAKE_FIR_FILTER(filter_11tap_1hz);

static float value_pressure = 0.0f;
static float value_pressure_raw = 0.0f;
static float value_temperature_1 = 0.0f;
static float value_temperature_2 = 0.0f;
static float value_flow_rate = 0.0f;
static float value_flow_volume = 0.0f;
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

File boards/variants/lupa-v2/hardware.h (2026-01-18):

#pragma once

//
// Input GPIOs
//

// Lever actuator input switch
// High = Lever open
// Low  = Lever closed or partially open
#define PIN_IN_LEVER 8

// Water tank low switch
// High = Water tank is low
//#define PIN_IN_WATER_LOW 22
#define PIN_IN_WATER_LOW 9

// Power button
#define PIN_IN_POWER_BTN 10

// Water flow pulse sensor input pin
// 5V-24V
// Pull-up
// Flow rate 0.75-1L/min
// https://www.eptsensor.com/flow-sensor/hall-flow-sensor/fm-hl3012-flow-meter-hall-sensor.html
#define FLOW1_PULSE_PIN 11
#define FLOW2_PULSE_PIN 12
// Note: D39 has stability issues, do not use for this.

// Boiler tank sensor (capsense/touch)
// Used for auto-fill logic
#define PIN_IN_WATER_FULL 4 // Touch0

//
// Output GPIOs
//

// Boiler heater element output (PWM)
#define PIN_OUT_HEAT 13

// Pump output (PWM)
#define PIN_OUT_PUMP 14

// Fill boiler solenoid output (On/Off)
//#define PIN_OUT_FILL_SOLENOID 5
#define PIN_OUT_FILL_SOLENOID 45


//
// I2C Bus
//
// [0x7F] : Pressure Transducer
//
#define I2C_SCL     46
#define I2C_SDA     47
//#define I2C_SCL1     46
#define I2C_SCL2     48 // 2nd transducer, shares SDA

// Pressure Transducer
// White: SDA
// Black: SCL
// Brown: 3.3V
// Blue:  GND
#define PRESSURE_I2C_ADDR (0x7F)

// Full-scale pressure reading
// Note: even though full scale pressure is 12 bar, 
// the actual full scale is 120 units.
// Pressure should read 1.0 bar when open to atmosphere.
#define PRESSURE_FULL_SCALE (120) // Bar x10


//
// SPI Bus 1 (HSPI)
// - LCD Left & Right
// SPI Bus 2 (VSPI)
// - MAX31865 RTD #1 & #2
//

#define MAX_RDY     40

#define MAX1_CS     38
#define MAX2_CS     39

#define RTD_NOMINAL_RESISTANCE (100)
#define RTD_REFERENCE_RESISTANCE (430)
#define RTD_MIN_TEMP (-200)
#define RTD_MAX_TEMP (400)


#define LEDC_CH_DISPLAY (0)
#define LEDC_CH_PUMP    (2)

#define UART_DEBUG_BAUD (115200)

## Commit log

2023-05-10 Move to TFT_eSPI and implement double buffering to prevent flicker
    [hardware.h, main.cpp]
2023-05-11 Add RST pin for TFT
2023-05-16 Fix MAX SPI configuration, detect non-responsive sensor
    [main.cpp]
2023-05-16 Update I2C configuration to avoid use of GPIO2, as this causes problems with flashing
    [hardware.h]
2023-05-17 Improve water flow readings, fix pressure scale
    [hardware.h, main.cpp]
2023-05-17 Filter pressure/temperature samples with FIR filter
2023-05-17 Update filters and improve pressure reading responsiveness
2023-05-17 Rename PressureTransducer.h
2023-05-17 Add gauges to sensor test view and adjust colors
2023-05-17 Update FIR filter taps to have a cleaner impulse response
2023-05-17 Rework UI and detect lever pull from water flow sensor
    [config.h, main.cpp]
2023-05-20 Calibrate thermocouple and provide grouphead estimate
2023-05-20 Improve temperature reading stability
    [SensorSampler.cpp, main.cpp]
2023-05-20 Implement PID control of boiler
2023-05-21 Update PID parameters
2023-05-21 Debounce brew timer
2023-05-21 Fix sleep idle timeout
    [Display.cpp, UIState.cpp, config.h]
2023-05-21 Fix temperature sensor glitching
    [SensorSampler.cpp]
2023-05-26 Configure device to not go to sleep after preheating
2023-05-26 Apply offset to heater PID when water is flowing
2023-05-28 Implement new PID algorithm
    - Uses floats
    - Allows perturbation of error to provide manual prediction
    - Caller is now responsible for calling at a regular tick rate (fits better with my architecture)
    [SensorSampler.cpp, UIState.cpp]
2023-06-05 WiFi no longer blocks initialization
    [config.h]
2023-06-05 Add HomeAssistant support for remote on/off and sensor reporting
2023-06-05 Continue reporting temperature when off
2023-06-11 Implement power button
2023-06-11 Estimate boiler power draw and report to HomeAssistant
2023-06-11 Fix sleep mode timeout
    [IO.cpp]
2023-06-12 Implement power off/on animation
2023-06-13 Rename HeatControl::setMode to setProfile, reorganize heat profile config
2023-06-13 Filter flowrate and rework SensorSampler
    [IO.cpp, SensorSampler.cpp, hardware.h]
2023-06-13 Add PID tuning mode, fix bug where heater gets stuck on at 1% power
    [SensorSampler.cpp]
2023-07-10 Add second flow meter and calibrate flow readings
2023-07-10 Detect firmware crash from reset reason
    [main.cpp]
2023-07-12 Implement hardware pump and water fill control
2023-07-12 Tidy up pump / fill logic state machine
2023-07-12 Set power-on state to off
2023-07-12 Disable WiFi power saving to improve connection reliability
2023-09-25 Update default boiler temperature presets
2023-09-25 Move preheat done check to Sensor Sampler
    Eventually will make this detect whether the temperature has stabilized
    [SensorSampler.cpp, main.cpp]
2023-09-25 Disable PID perturbation as it is making the PID overshoot too much
2023-10-02 Turn off water level sensor in standby to prevent corrosion of metal probe
    [IO.cpp]
2023-12-01 Experiment in attempt to isolate crashes
    [Display.cpp, IO.cpp, SensorSampler.cpp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]
2023-12-01 Fix pump not turning off when tank runs empty
2023-12-01 Fix display turning off if power button pressed rapidly
2023-12-01 Implement pressure stabilization routine to keep water loop filled
2023-12-02 Report pressure sensor to HomeAssistant, change sample rate to 5s
2024-01-26 Fix crash due to timer reset
    [SensorSampler.cpp]
2024-01-27 Actually fix crash due to timer not rearming
    Somehow calling touch_pad_filter_stop() interferes with the FreeRTOS timer queue, preventing the SensorSampler timer from being able to be re-armed.
    [IO.cpp, SensorSampler.cpp]
2024-03-22 Fix watchdog triggering on startup if init takes too long
    [main.cpp]
2024-03-22 Fix water tank low signal being unstable while reading RTD sensor
    [IO.cpp]
2024-03-22 Fix glitches in display brightness during power on/off animation
    [Display.cpp]
2024-03-22 Fix boiler low signal briefly asserting during power on
    [IO.cpp]
2024-03-22 Disable internal temperature sensor reading, it is not useful
2024-03-22 Add pressure PID control
2024-03-23 Fine tune PID algorithm to ensure stable control of pump pressure
2024-03-23 Add failsafe recovery path since I'm so good at finding fatal bugs in the ESP32
    [main.cpp]
2024-03-23 Add copy of schematic
2024-03-24 Tidy up MQTT config parameters and pump control code
2024-03-24 Ensure fault UI is shown in failsafe mode
    [main.cpp]
2024-03-24 Disable PCNT timer as it causes severe issues (when I least expect it)
2024-03-24 Fix error when trying to set pump state before LEDC is initialized
    [IO.cpp]
2024-03-24 Clean up HeatController and move PWM to IO namespace
2024-03-24 Restrict PID integral accumulator when output is being driven negative
2024-03-24 Add config parameters for target temp/pressure
2024-05-03 Update default PID coefficients for boiler
2024-05-06 Avoid calling network tasks if WiFi is not connected
    [main.cpp]
2024-06-03 Change temperature defaults for better brew
2024-06-08 Fix flow rate measurement
    [SensorSampler.cpp]
2024-06-09 Add second RTD sensor to measure main boiler
2024-06-10 Display PID terms on display graph for debug
2024-06-10 Fix heater output ceasing to function
    [IO.cpp]
2024-07-08 Fix glitch in boiler PWM output
    [IO.cpp]
2024-07-09 Add icons for wifi status and background image
    NOTE: background image reduces framerate quite a bit, may need to remove for performance.
2024-11-29 Update default PID parameters
2024-11-29 Fix invalid power meter readings
    [IO.cpp]
2024-12-22 Prevent message from being repeatedly printed to debug port
    [Display.cpp]
2024-12-23 Fix pump sometimes not triggering when lever pulled
2025-12-01 Pin package versions, improve missing sensor handling, update comments
    [IO.cpp, PressureTransducer.cpp, SensorSampler.cpp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]
2025-12-01 Add PCB design files
    [lupa-B_Cu.gbr, lupa-B_Mask.gbr, lupa-B_Silkscreen.gbr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]
2025-12-01 Update BOM
    [lupa.csv, lupa.kicad_pcb, lupa.kicad_sch]
2026-01-16 Migrate to Arduino Core 3.x, add support for ESP32-S3 board
2026-01-18 Minimal functionality working on ESP32-S3
    Webserver disabled due to crash, sensors not yet tested
    [Display.cpp, IO.cpp, SensorSampler.cpp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]
2026-01-20 Use board variants for IO pin mapping, compiles now for both variants
    [partitions-16M.csv, partitions-8M.csv]
2026-01-20 Implement brew profiling logic
    Supports code-defined brewing profiles for both pressure and flow-rate regulated modes
2026-01-21 Fix issues running on LupaV1
    [Display.cpp, IO.cpp, main.cpp]
2026-01-22 Fix partition table for LupaV1 (Using N4 variant)
    [partitions-16M.csv, partitions-4M.csv, partitions-8M.csv]
2026-01-22 Fix heater not turning off edge case
2026-01-23 Replace usage of Wire.h with native ESP I2C driver
    [IO.cpp, PressureTransducer.cpp, main.cpp]
2026-01-23 Rework web interface and optimize memory usage
    [main.cpp]
2026-01-24 Add heap logging to track down allocations
2026-01-24 Rework sensor sampler for better sampling reliability
    Moved all sampling out of timers into a dedicated high priority task -
    this works much better and ensures other tasks won't block sampling
    [PressureTransducer.cpp, SensorSampler.cpp]
2026-01-27 Revamp Brew control loop - no longer using PID, more stable
    [SensorSampler.cpp, main.cpp]
2026-01-27 Rework display update to work with reduced RAM
    Something changed in Arduino 3.x.x and now there is no longer enough heap to allocate both buffers without external PSRAM...
    I tried hacking around this, but it caused severe stability problems in the ESP stack.
    So, the only alternatives are to either use a PSRAM part or only use one buffer and alternate between drawing left & right.
    [Display.cpp]
